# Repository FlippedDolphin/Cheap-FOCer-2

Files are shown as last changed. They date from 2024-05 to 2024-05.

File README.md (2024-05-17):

# Cheap FOCer 2 (v1.0)

Low-Cost(around $120 for 5 boards and components) Motor Controller based on the VESC 6

***** caution *******

This is a custom VESC for OpenFFBoard based On Cheap FOCer 2(v1.0)

* Replaced the shunt registers for low current.

* Removed the useless IMU.

* Cleaned up HALL/Encoder lines(for ABN) and COMM lines(for BiSS-C)
  for high frequency signals.(I tested COMM lines only.)

* Added OVP(over voltage protector) for PSU usage.

* Added POWER and MOTOR connector for easy plug.

* Max voltage 50V and max current is 14A.

U8 and J11 are unused, just for test purpose.

I placed JST connector for USB connection(USB1). The normal USB-C connector is J2, but it costs a little more. You can select J2/USB1(If use USB1, you need a converter from USB I/F to JST PH connector. I used cheap USB hub pcb).

A sample BOM and Position are in prodction folder.

bom.org.csv and position.org.csv are come from KiCad.

I used bom.csv and bom.lcsc.csv to order JLCPCB and LCSC respectively.

When I ordered the PCB and parts, I have already had some parts, so my order is minimum.
You need adjust the BOMS for your needs.

I used position.csv for JLCPCB order because original one from Kicad has errors for some parts. You need to check the position when you order yours.

## Warning

* This board has been bench tested with MIGE motor(130st-m10010 and 90ST-M04025) and BiSS-C encoder.
 Hardware or firmware flaws could still exist and affect user operation.
* You are liable for any and all controllers built using this design. This product is intended for hobbyists and not intended for commercial use.
* Do not ask the original auther of Cheap FOCer 2 about this board. He has no responsibility about this board at all.

Licens is followd by the parent project.

## Firmware

The firmware for this board is my bdlc repository with branch "Custom_CFOC2_OpenFFBoard". The Target is "Cheap_FOCer_2_005_nl".

***** caution *******

Front and Back:

 

Pin outs:


## License

Cheap FOCer 2 is licensed under the Creative Commons Attribution-ShareAlike 4.0 International License. To view a copy of this license, visit <http://creativecommons.org/licenses/by-sa/4.0/.>

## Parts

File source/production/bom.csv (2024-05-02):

Designator | Footprint | Quantity | Value | LCSC Part #
C1 | C0603 | 1 | 100nF | C14663
C10, C14 | 603 | 2 | 15p | C1644
C11, C13, C15, C16, C17, C18, C19, C47, C7, C8, C9 | 603 | 11 | 2.2u | C23630
C12, C2, C20, C24, C35, C43, C6 | 603 | 7 | 100n | C14663
C21, C23, C26, C28, C39, C4, C40, C66, C67 | 603 | 9 | 1nF | C1588
C22, C25, C30, C32, C44 | 603 | 5 | 2.2uF | C23630
C27 | 603 | 1 | 6.8n | C1631
C29 | 603 | 1 | 150p | C1594
C3 | 603 | 1 | .01uF | C57112
C31 | 603 | 1 | 22n | C21122
C33, C42 | 1210 | 2 | 4.7uF, 100V | C385986
C34 | 603 | 1 | 15nF | C1596
C36, C37, C38, C41 | 603 | 4 | 220n | C21120
C45, C46, C48, C49, C50, C51 | 805 | 6 | 22uf | C45783
C5 | 603 | 1 | 0.1u | C14663
C52, C53, C59, C60 | 603 | 4 | 2.2nF | C1604
C55, C56, C63, C64, C68, C69 | 805 | 6 | 4.7nF, 100V | C565636
C58, C61, C62 | 2220 | 3 | 10uF, 100V | C153035
C70, C71 | C1206 | 2 | 22uF | C77091
D1, D2 | SOT-363_SC-70-6 | 2 | SMF05CT1G | C15879
D10, D11, D12, D13, D14, D15 | D_SOD-323 | 6 | D_Schottky | C313457
D16 | SMA_L4.3-W2.6-LS5.2-RD | 1 | SS34 | C8678
D3 | 603 | 1 | RED | C2286
D4 | 603 | 1 | GRN | C72043
D5 | 603 | 1 | BLU | C965807
D6 | D_SMA | 1 | 100v, 1A | C224219
D7 | D_SMB | 1 | D_TVS | C78395
D8 | TO-220-2_Horizontal_TabUp | 1 | STTH3010DTO-220AC_STM | C73865
D9 | SODFL3618X110N | 1 | GOODWORK K110 | C908663
L1 | L_Taiyo-Yuden_NR-60xx_HandSoldering | 1 | 22u | C266430
L2 | IND-SMD_L7.0-W6.8 | 1 | 22uH | C27442
NTC1 | 603 | 1 | NTC 10k | C76589
Q10, Q11, Q2, Q3, Q6, Q7 | SOT-23 | 6 | Q_PNP_BCE | C8542
R1, R2 | R0603 | 2 | 5.1k | C23186
R10, R15, R16, R17, R29, R37, R39, R41, R5 | 603 | 9 | 2k2 | C4190
R11, R8, R9 | 603 | 3 | 100R | C22775
R12, R13 | 603 | 2 | 60 | C25196
R14, R18, R19, R20, R22, R23, R30, R32 | 603 | 8 | 10k | C25804
R21, R33, R34 | 603 | 3 | 1.5k | C22843
R24, R25, R31 | 603 | 3 | 1k | C21190
R26 | 603 | 1 | 3.3k | C22978
R27 | 603 | 1 | 18k | C25810
R28 | 603 | 1 | 15k | C22809
R3 | 603 | 1 | 0R | C3017805
R35 | 603 | 1 | 220k | C22961
R36, R38, R4, R40 | 603 | 4 | 39k | C23153
R42, R44 | RESC2012X65 | 2 | 20k | C114233
R43, R45 | RESC2012X65 | 2 | 1k | C100046
R46, R47, R49, R86 | RESC2012X65 | 4 | 10k | C100047
R48, R89 | RESC2012X65 | 2 | 560 | C137421
R50, R51, R62, R63, R74, R75 | 603 | 6 | 4.7R | C23164
R52, R53, R64, R65, R76, R77 | 805 | 6 | 4.7R | C17675
R54, R55, R66, R67, R78, R79 | 603 | 6 | 4.7k | C23162
R56, R57, R68, R69, R80, R81 | R_2512_Yageo_big_pads | 6 | 0.01R | C2903468
R58, R59, R60, R61, R70, R71, R72, R73, R82, R83, R84, R85 | 805 | 12 | 10R | C17415
R6, R7 | 603 | 2 | 22R | C23345
R87 | RESC2012X65 | 1 | 62K | C137415
R88 | RESC2012X65 | 1 | 3k3 | C114222
U1 | SOIC-8_3.9x4.9mm_P1.27mm | 1 | TJA1051T/3/1J | C38695
U2 | LQFP-64_10x10mm_P0.5mm | 1 | STM32F405RGT6 | C15742
U3 | SOIC-8_3.9x4.9mm_P1.27mm | 1 | TP2604-SR | C126446
U4 | HTSSOP-56-1EP_6.1x14mm_P0.5mm_EP3.61x6.35mm | 1 | DRV8301 | C98969
U5 | SOT-223-3_TabPin2 | 1 | AMS1117-3.3 | C6186
U7 | SOT-23-6_L2.9-W1.6-P0.95-LS2.8-BL(MT3608) | 1 | MT3608 | C84817
X1 | Crystal_SMD_5032-2Pin_5.0x3.2mm | 1 | 8MHz 10ppm (X50328MSB2GI) | C115962

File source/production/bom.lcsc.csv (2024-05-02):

Designator | Footprint | Quantity | Value | LCSC Part # | Bottom | 所有
C54, C57, C65 | CP_10x20mm_hor_with_model_mirrored_less_silk | 3 | 330u, 63V | C437643
D8 | TO-220-2_Horizontal_TabUp | 1 | STTH3010DTO-220AC_STM | C73865
J4 | CONN-TH_2P-P5.08_1757242 | 1 | Conn_01x02 | C90074
J8 | CONN-TH_MSTBA2.5-4-G-5.08 | 1 | MotorPower | C90076
Q1 | TO-247-3_Horizontal_TabUp | 1 | FGH40N60SFDTU | C49514
Q10, Q11, Q2, Q3, Q6, Q7 | SOT-23 | 6 | Q_PNP_BCE | C8542
Q12, Q13, Q4, Q5, Q8, Q9 | TO-220-3_Horizontal_TabUp_no_hole | 6 | NCEP60T20 | C284868

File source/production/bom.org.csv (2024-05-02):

Designator | Footprint | Quantity | Value | LCSC Part #
C1 | C0603 | 1 | 100nF | C14663
C10, C14 | 0603 | 2 | 15p | C1644
C11, C13, C15, C16, C17, C18, C19, C47, C7, C8, C9 | 0603 | 11 | 2.2u | C23630
C12, C2, C20, C24, C35, C43, C6 | 0603 | 7 | 100n | C14663
C21, C23, C26, C28, C39, C4, C40, C66, C67 | 0603 | 9 | 1nF | C1588
C22, C25, C30, C32, C44 | 0603 | 5 | 2.2uF | C23630
C27 | 0603 | 1 | 6.8n | C1631
C29 | 0603 | 1 | 150p | C1594
C3 | 0603 | 1 | .01uF | C57112
C31 | 0603 | 1 | 22n | C21122
C33, C42 | 1210 | 2 | 4.7uF, 100V | C385986
C34 | 0603 | 1 | 15nF | C1596
C36, C37, C38, C41 | 0603 | 4 | 220n | C21120
C45, C46, C48, C49, C50, C51 | 0805 | 6 | 22uf | C45783
C5 | 0603 | 1 | 0.1u | C14663
C52, C53, C59, C60 | 0603 | 4 | 2.2nF | C1604
C54, C57, C65 | CP_10x20mm_hor_with_model_mirrored_less_silk | 3 | 330u, 63V | C437643
C55, C56, C63, C64, C68, C69 | 0805 | 6 | 4.7nF, 100V | C565636
C58, C61, C62 | 2220 | 3 | 10uF, 100V | C153035
C70, C71 | C1206 | 2 | 22uF | C77091
D1, D2 | SOT-363_SC-70-6 | 2 | SMF05CT1G | C15879
D10, D11, D12, D13, D14, D15 | D_SOD-323 | 6 | D_Schottky | C313457
D16 | SMA_L4.3-W2.6-LS5.2-RD | 1 | SS34 | C8678
D3 | 0603 | 1 | RED | C2286
D4 | 0603 | 1 | GRN | C72043
D5 | 0603 | 1 | BLU | C965807
D6 | D_SMA | 1 | 100v, 1A | C224219
D7 | D_SMB | 1 | D_TVS | C78395
D8 | TO-220-2_Horizontal_TabUp | 1 | STTH3010DTO-220AC_STM | C73865
D9 | SODFL3618X110N | 1 | GOODWORK K110 | C908663
F1, F2, F3 | Fiducial_1mm_Dia_2mm_Outer | 3 | Fiducial
H1, H2, H3, H4_3, H4_2, H4, H5, H6 | MountingHole_3.2mm_M3_ISO14580_Pad | 8 | MountingHole
H7 | Sam_J | 1 | SLJ
H8 | OSHW-Logo2_9.8x8mm_SilkScreen | 1 | Open Hardware Logo
H9 | KiCad-Logo2_5mm_SilkScreen | 1 | KiCAD Logo
J1 | JST_PH_B7B-PH-K_1x07_P2.00mm_Vertical | 1 | Conn_01x07
J10 | JST_PH_B2B-PH-K_1x02_P2.00mm_Vertical | 1 | On/Off
J11 | CONN-TH_1755736 | 1 | VESC_Vin | C480503
J12 | JST_PH_B2B-PH-K_1x02_P2.00mm_Vertical | 1 | PWR LED
J13 | JST_PH_S2B-PH-K_1x02_P2.00mm_Horizontal | 1 | E-Stop
J2 | GCT_USB4105-GF-A | 1 | USB4105-GF-A | C319148
J3, J7 | JST_PH_B2B-PH-K_1x02_P2.00mm_Vertical | 2 | Conn_01x02
J4 | CONN-TH_2P-P5.08_1757242 | 1 | Conn_01x02 | C90074
J5 | JST_PH_B3B-PH-K_1x03_P2.00mm_Vertical_hybrid | 1 | Conn_01x03
J6 | PinHeader_1x02_P2.54mm_Vertical | 1 | Conn_01x03
J8 | CONN-TH_MSTBA2.5-4-G-5.08 | 1 | MotorPower | C90076
J9 | PinHeader_2x05_P2.00mm_Vertical | 1 | UNUSED MCU PINS
JP1 | SolderJumper-3_P1.3mm_Open_RoundedPad1.0x1.5mm_NumberLabels | 1 | SolderJumper_3_Open
L1 | L_Taiyo-Yuden_NR-60xx_HandSoldering | 1 | 22u | C266430
L2 | IND-SMD_L7.0-W6.8 | 1 | 22uH | C27442
NT1, NT2, NT3, NT4, NT5, NT6 | NetTie-2_SMD_Pad0.5mm | 6 | Net-Tie_2
NTC1 | 0603 | 1 | NTC 10k | C76589
P1 | JST_PH_B6B-PH-K_1x06_P2.00mm_Vertical | 1 | HALL/Encoder
P2 | JST_PH_B5B-PH-K_1x05_P2.00mm_Vertical | 1 | Conn_01x05_PH_SWIO
Q1 | TO-247-3_Horizontal_TabUp | 1 | FGH40N60SFDTU | C49514
Q10, Q11, Q2, Q3, Q6, Q7 | SOT-23 | 6 | Q_PNP_BCE | C8542
Q12, Q13, Q4, Q5, Q8, Q9 | TO-220-3_Horizontal_TabUp_no_hole | 6 | NCEP60T20 | C284868
R1, R2 | R0603 | 2 | 5.1k | C23186
R10, R15, R16, R17, R29, R37, R39, R41, R5 | 0603 | 9 | 2k2 | C4190
R11, R8, R9 | 0603 | 3 | 100R | C22775
R12, R13 | 0603 | 2 | 60 | C25196
R14, R18, R19, R20, R22, R23, R30, R32 | 0603 | 8 | 10k | C25804
R21, R33, R34 | 0603 | 3 | 1.5k | C22843
R24, R25, R31 | 0603 | 3 | 1k | C21190
R26 | 0603 | 1 | 3.3k | C22978
R27 | 0603 | 1 | 18k | C25810
R28 | 0603 | 1 | 15k | C22809
R3 | 0603 | 1 | 0R | C3017805
R35 | 0603 | 1 | 220k | C22961
R36, R38, R4, R40 | 0603 | 4 | 39k | C23153
R42, R44 | RESC2012X65 | 2 | 20k | C114233
R43, R45 | RESC2012X65 | 2 | 1k | C100046
R46, R47, R49, R86 | RESC2012X65 | 4 | 10k | C100047
R48, R89 | RESC2012X65 | 2 | 560 | C137421
R50, R51, R62, R63, R74, R75 | 0603 | 6 | 4.7R | C23164
R52, R53, R64, R65, R76, R77 | 0805 | 6 | 4.7R | C17675
R54, R55, R66, R67, R78, R79 | 0603 | 6 | 4.7k | C23162
R56, R57, R68, R69, R80, R81 | R_2512_Yageo_big_pads | 6 | 0.01R | C2903468
R58, R59, R60, R61, R70, R71, R72, R73, R82, R83, R84, R85 | 0805 | 12 | 10R | C17415
R6, R7 | 0603 | 2 | 22R | C23345
R87 | RESC2012X65 | 1 | 62K | C137415
R88 | RESC2012X65 | 1 | 3k3 | C114222
TP1 | TP1X01 | 1 | 12V
TP2 | TP1X01 | 1 | BR-
TP3 | TP1X01 | 1 | BR+
U1 | SOIC-8_3.9x4.9mm_P1.27mm | 1 | TJA1051T/3/1J | C38695
U2 | LQFP-64_10x10mm_P0.5mm | 1 | STM32F405RGT6 | C15742
U3 | SOIC-8_3.9x4.9mm_P1.27mm | 1 | TP2604-SR | C126446
U4 | HTSSOP-56-1EP_6.1x14mm_P0.5mm_EP3.61x6.35mm | 1 | DRV8301 | C98969
U5 | SOT-223-3_TabPin2 | 1 | AMS1117-3.3 | C6186
U6 | DIP794W45P254L959H508Q8 | 1 | LM358P | C5213
U7 | SOT-23-6_L2.9-W1.6-P0.95-LS2.8-BL(MT3608) | 1 | MT3608 | C84817
U8 | MT3068_Module | 1 | MT3608_Modle
USB1 | CONN-TH_B3B-PH-K-S | 1 | Conn_01x03 | C131339
X1 | Crystal_SMD_5032-2Pin_5.0x3.2mm | 1 | 8MHz 10ppm (X50328MSB2GI) | C115962

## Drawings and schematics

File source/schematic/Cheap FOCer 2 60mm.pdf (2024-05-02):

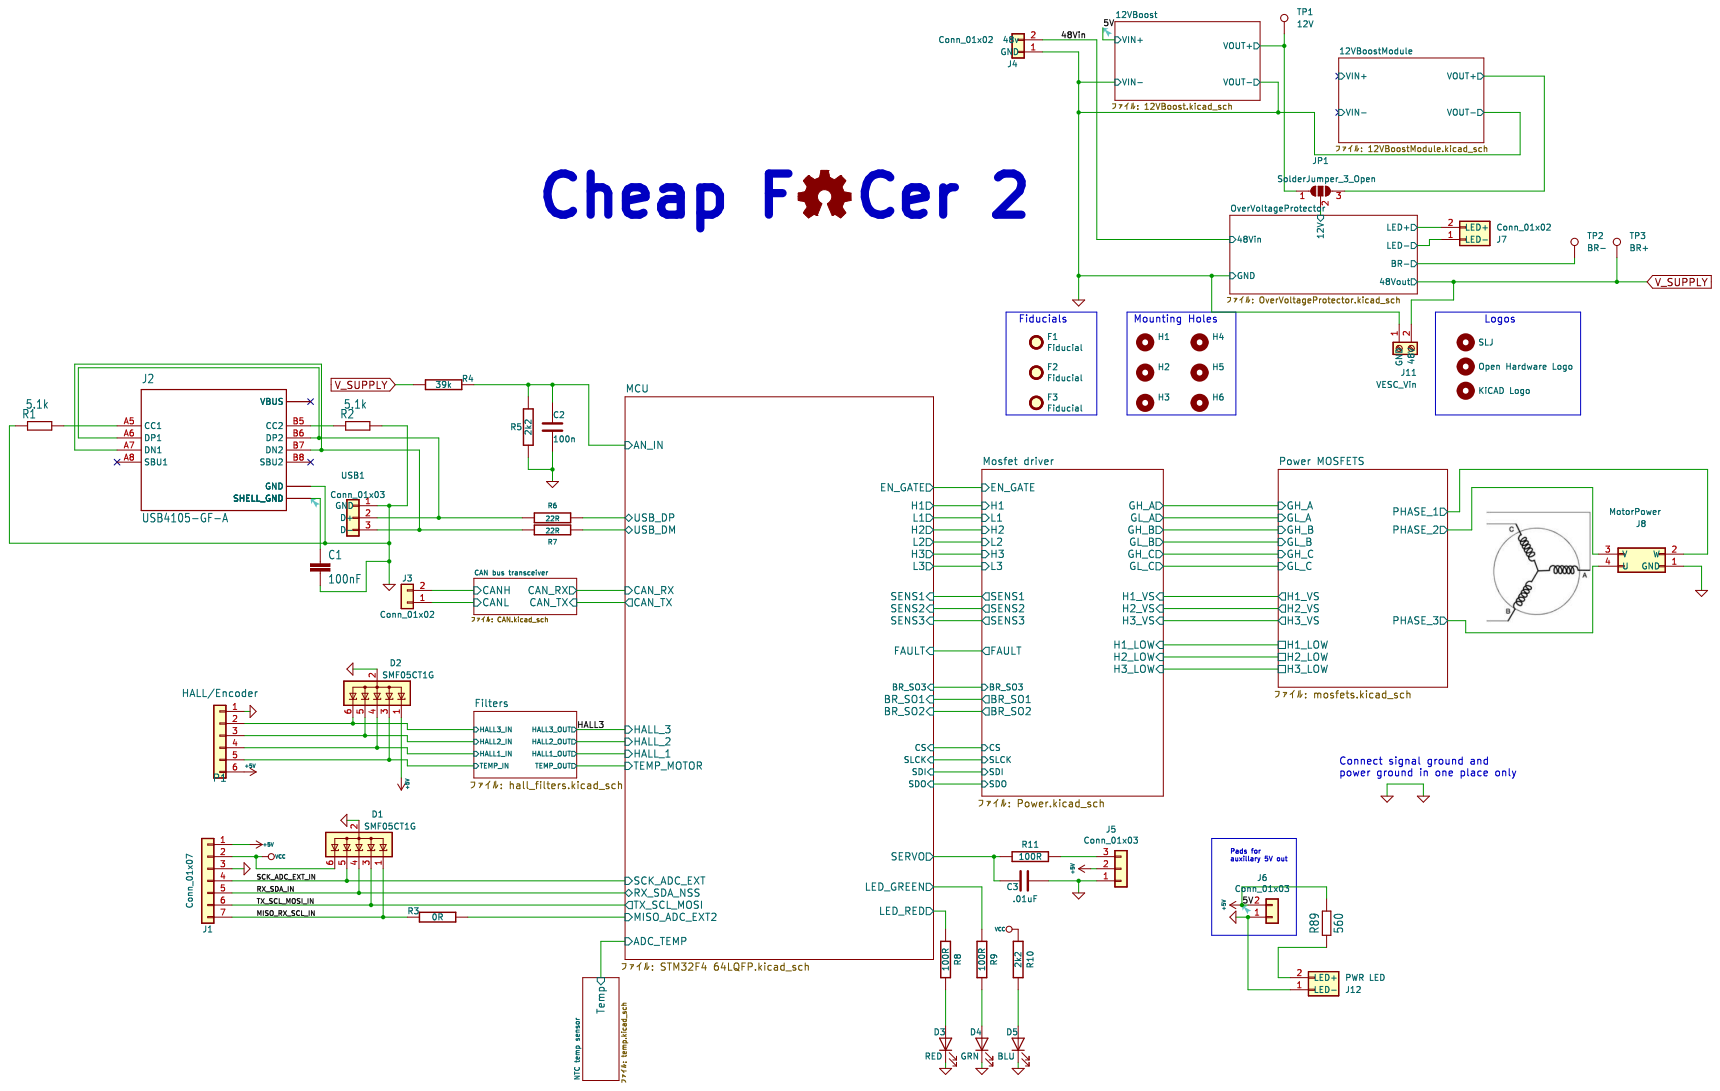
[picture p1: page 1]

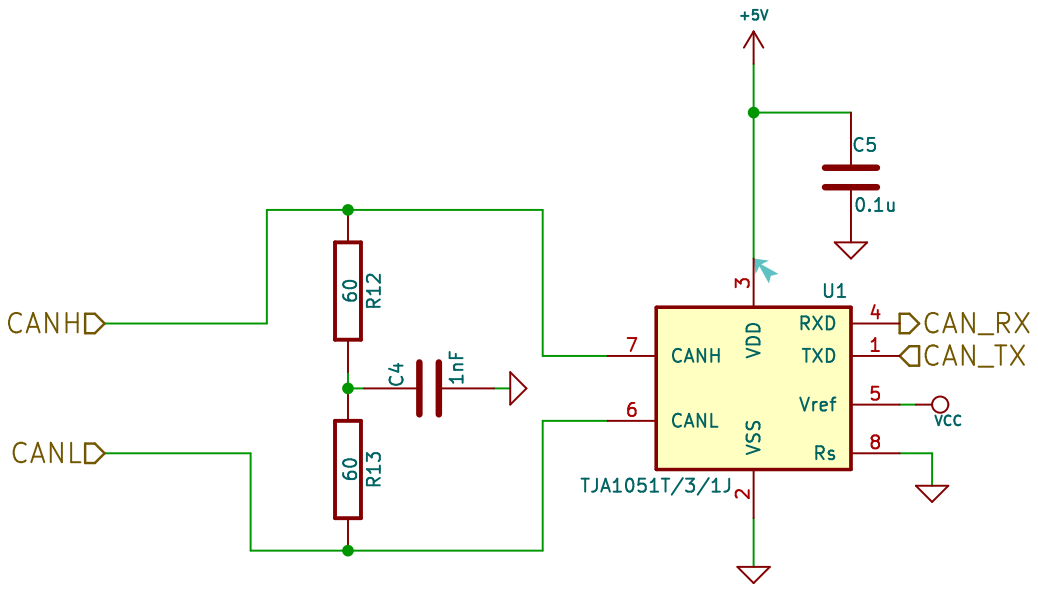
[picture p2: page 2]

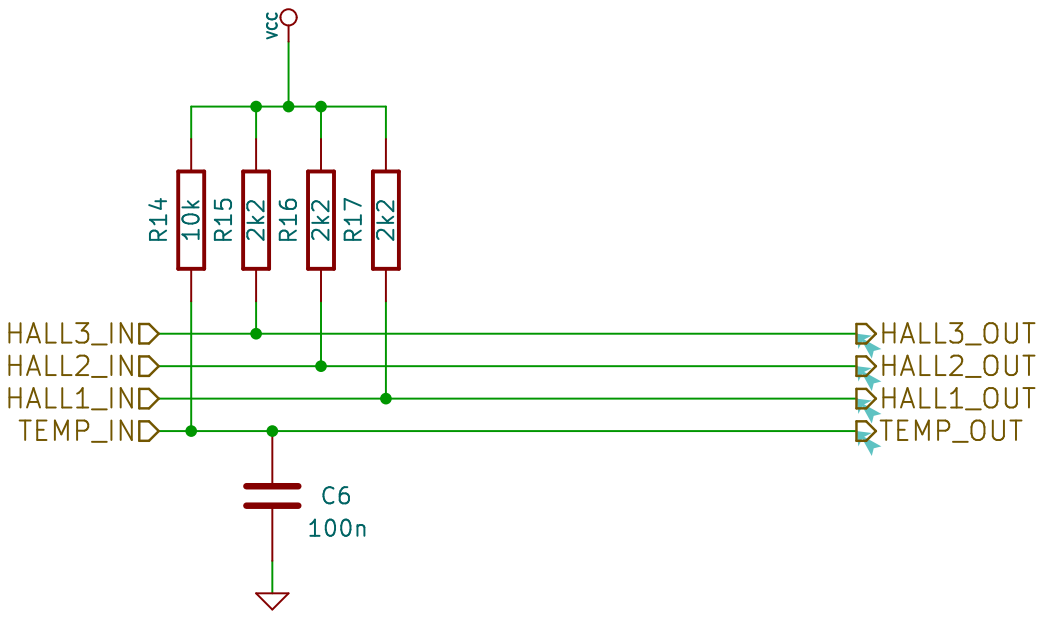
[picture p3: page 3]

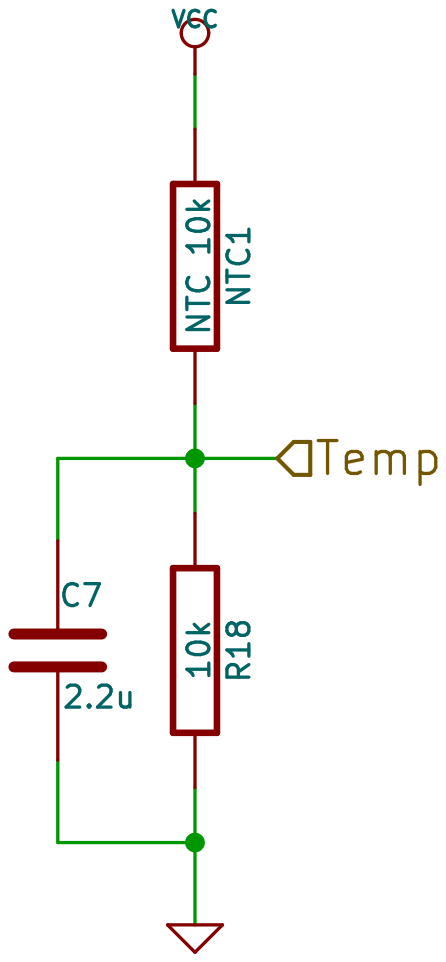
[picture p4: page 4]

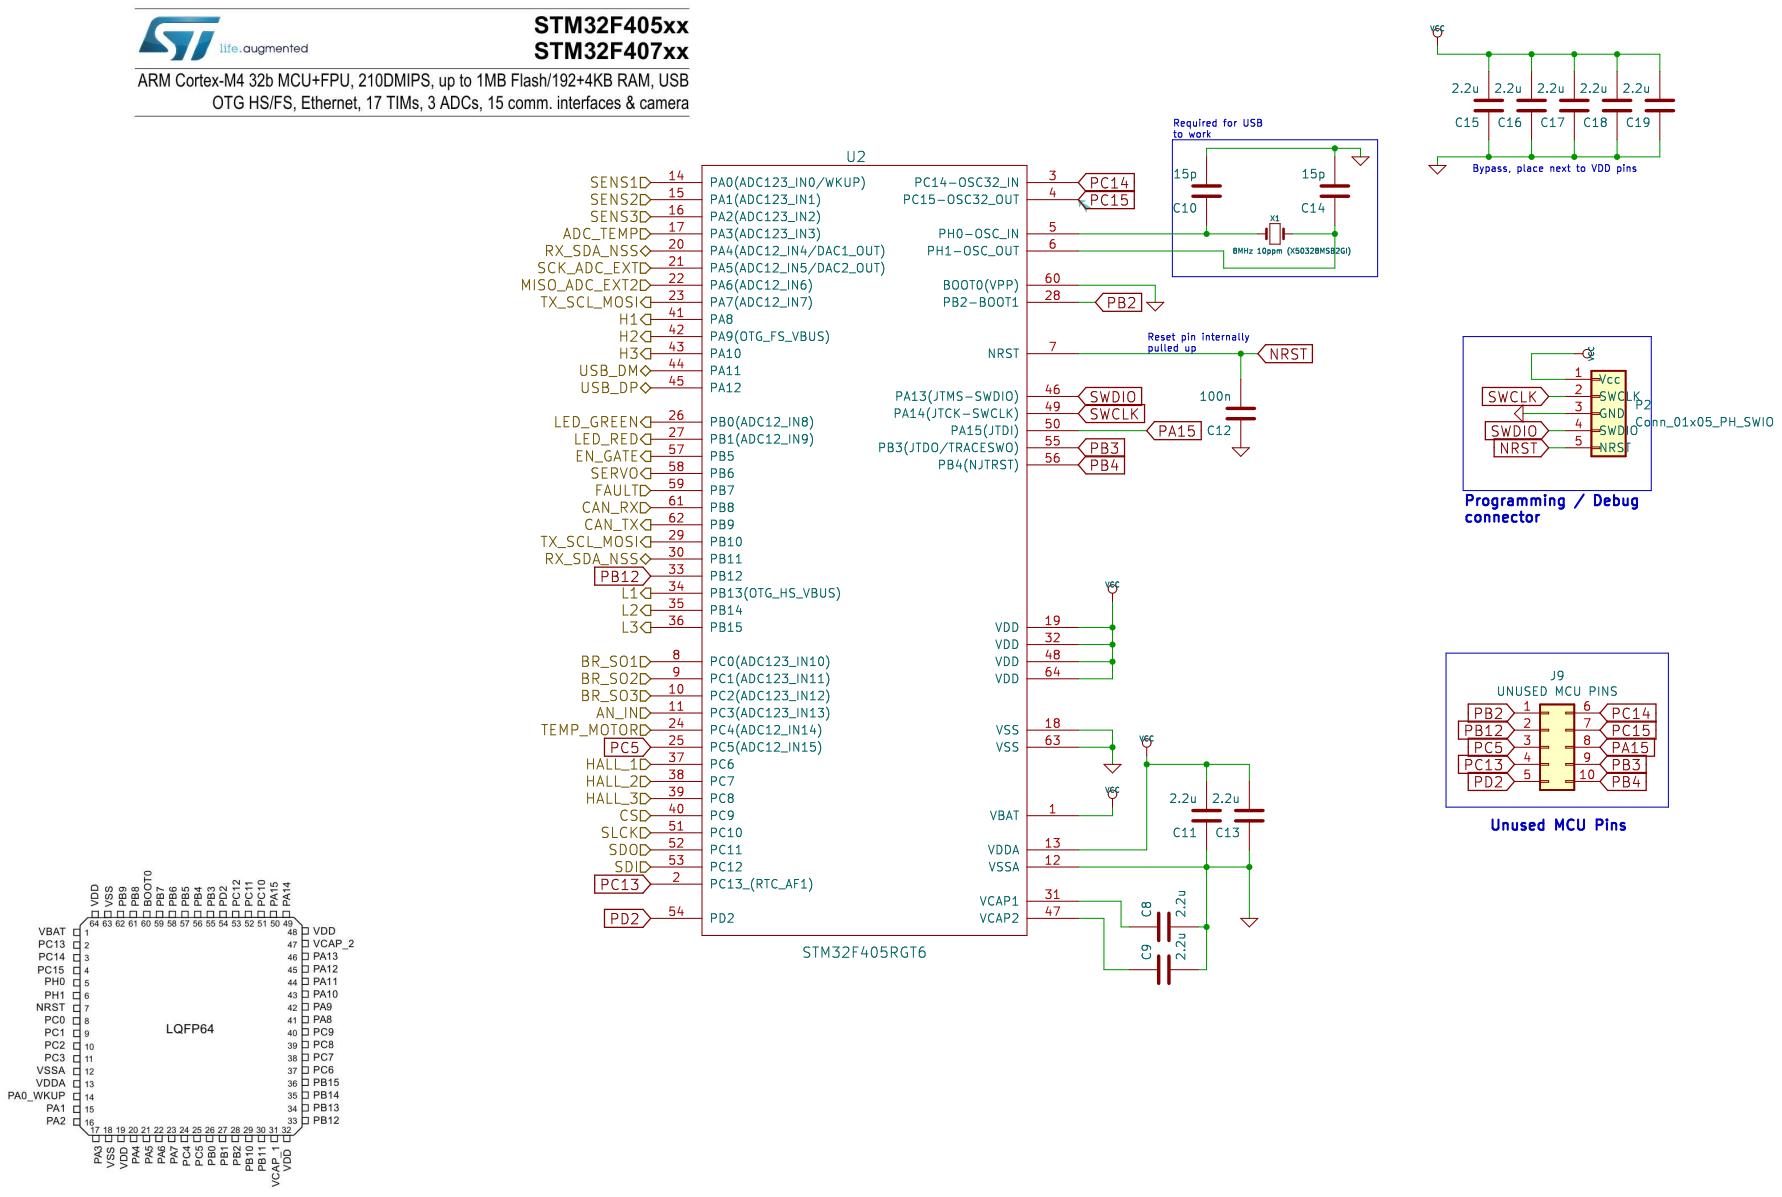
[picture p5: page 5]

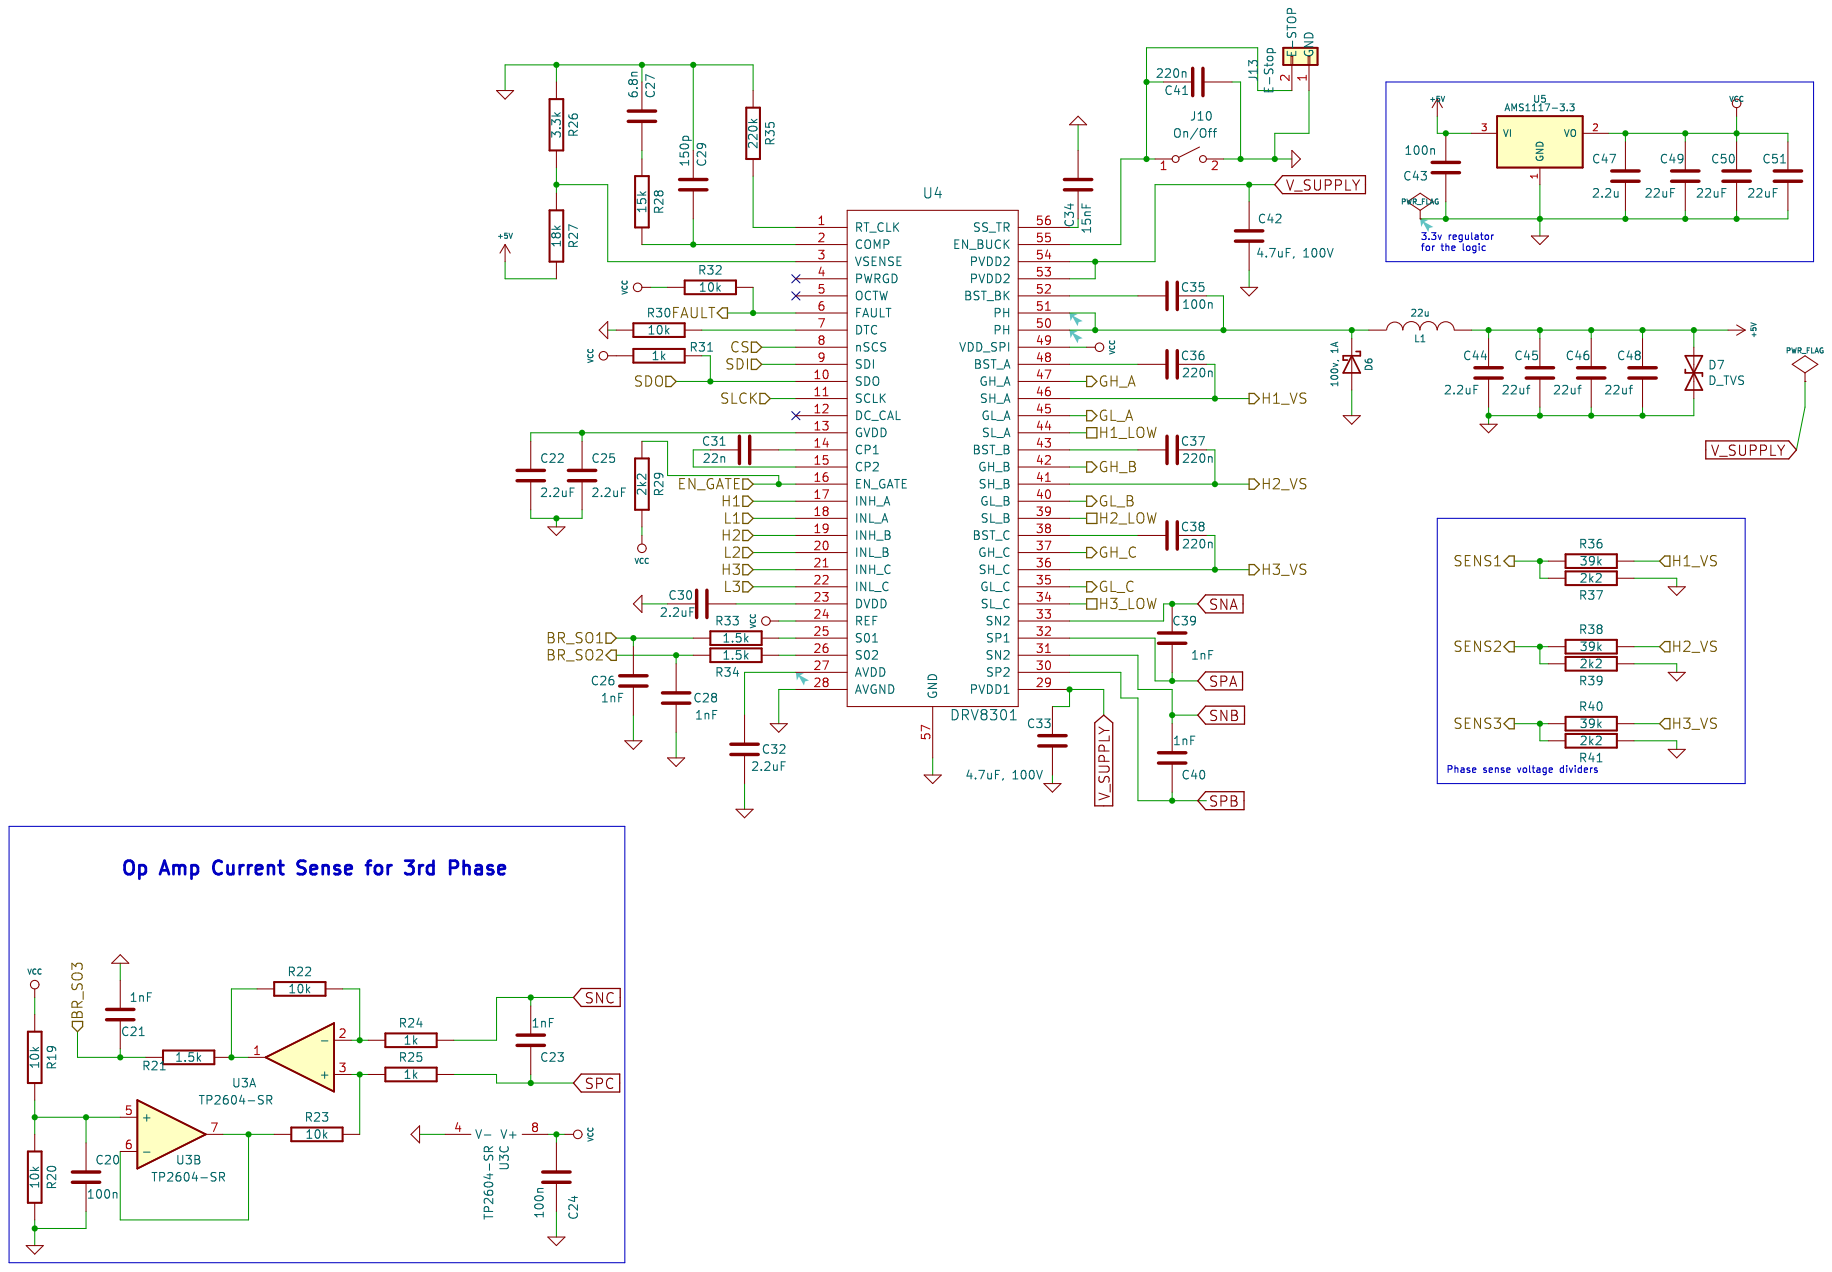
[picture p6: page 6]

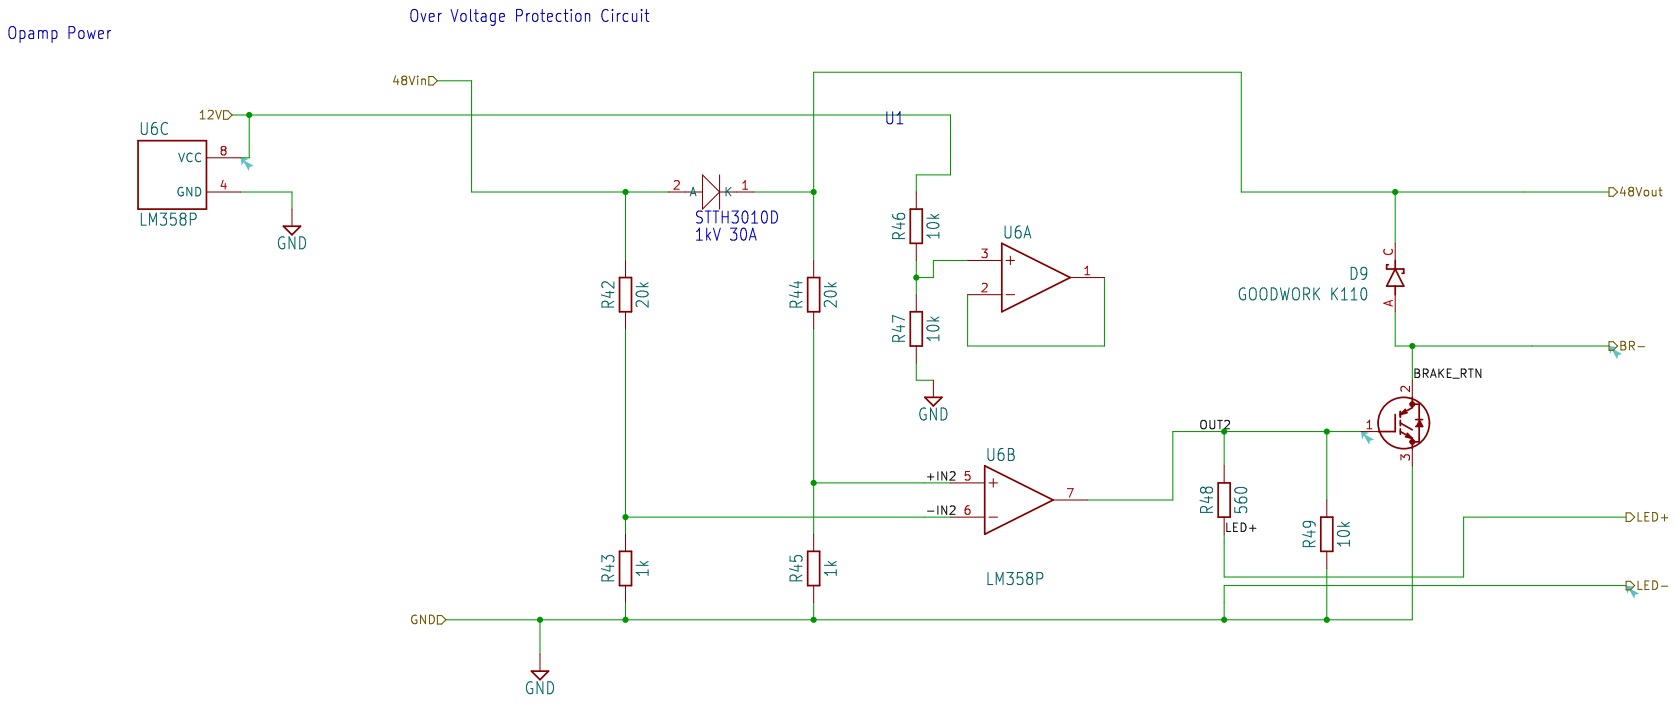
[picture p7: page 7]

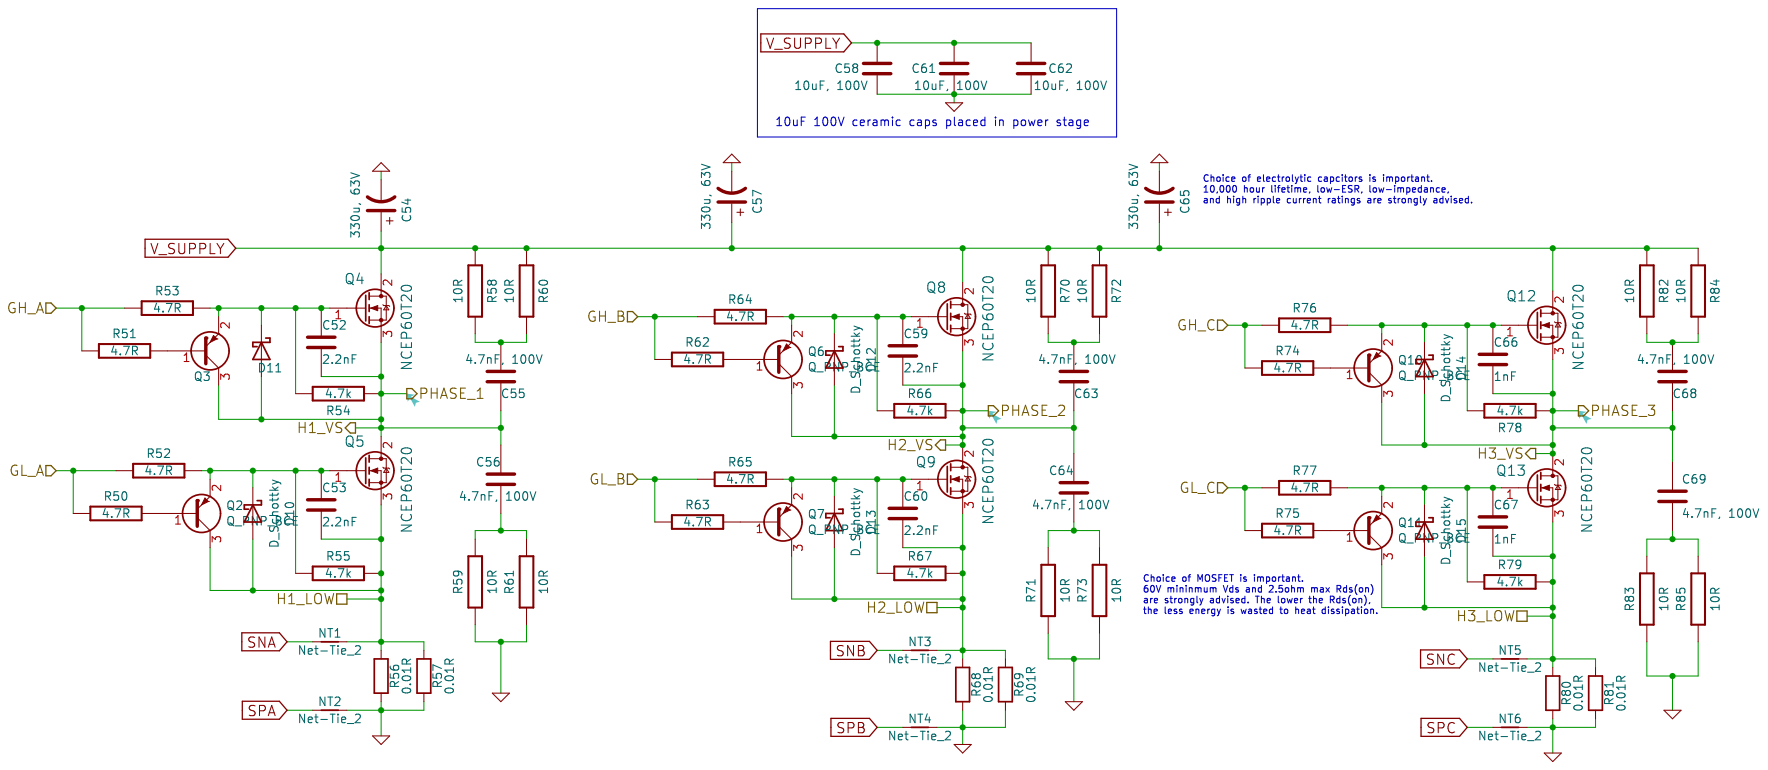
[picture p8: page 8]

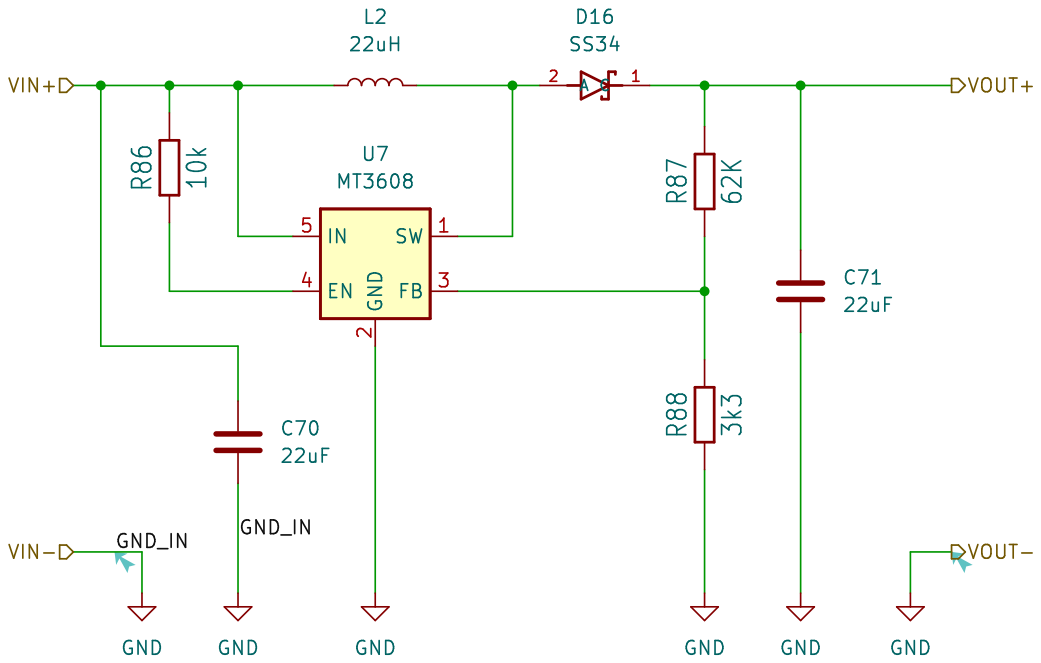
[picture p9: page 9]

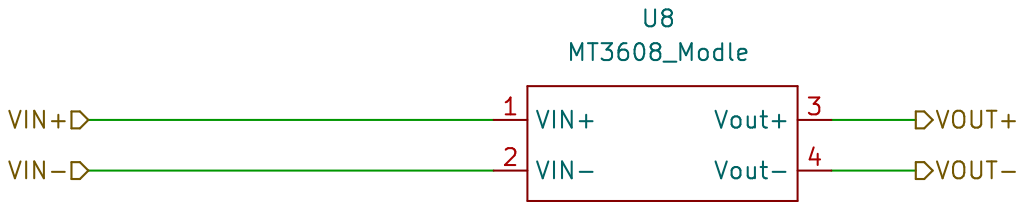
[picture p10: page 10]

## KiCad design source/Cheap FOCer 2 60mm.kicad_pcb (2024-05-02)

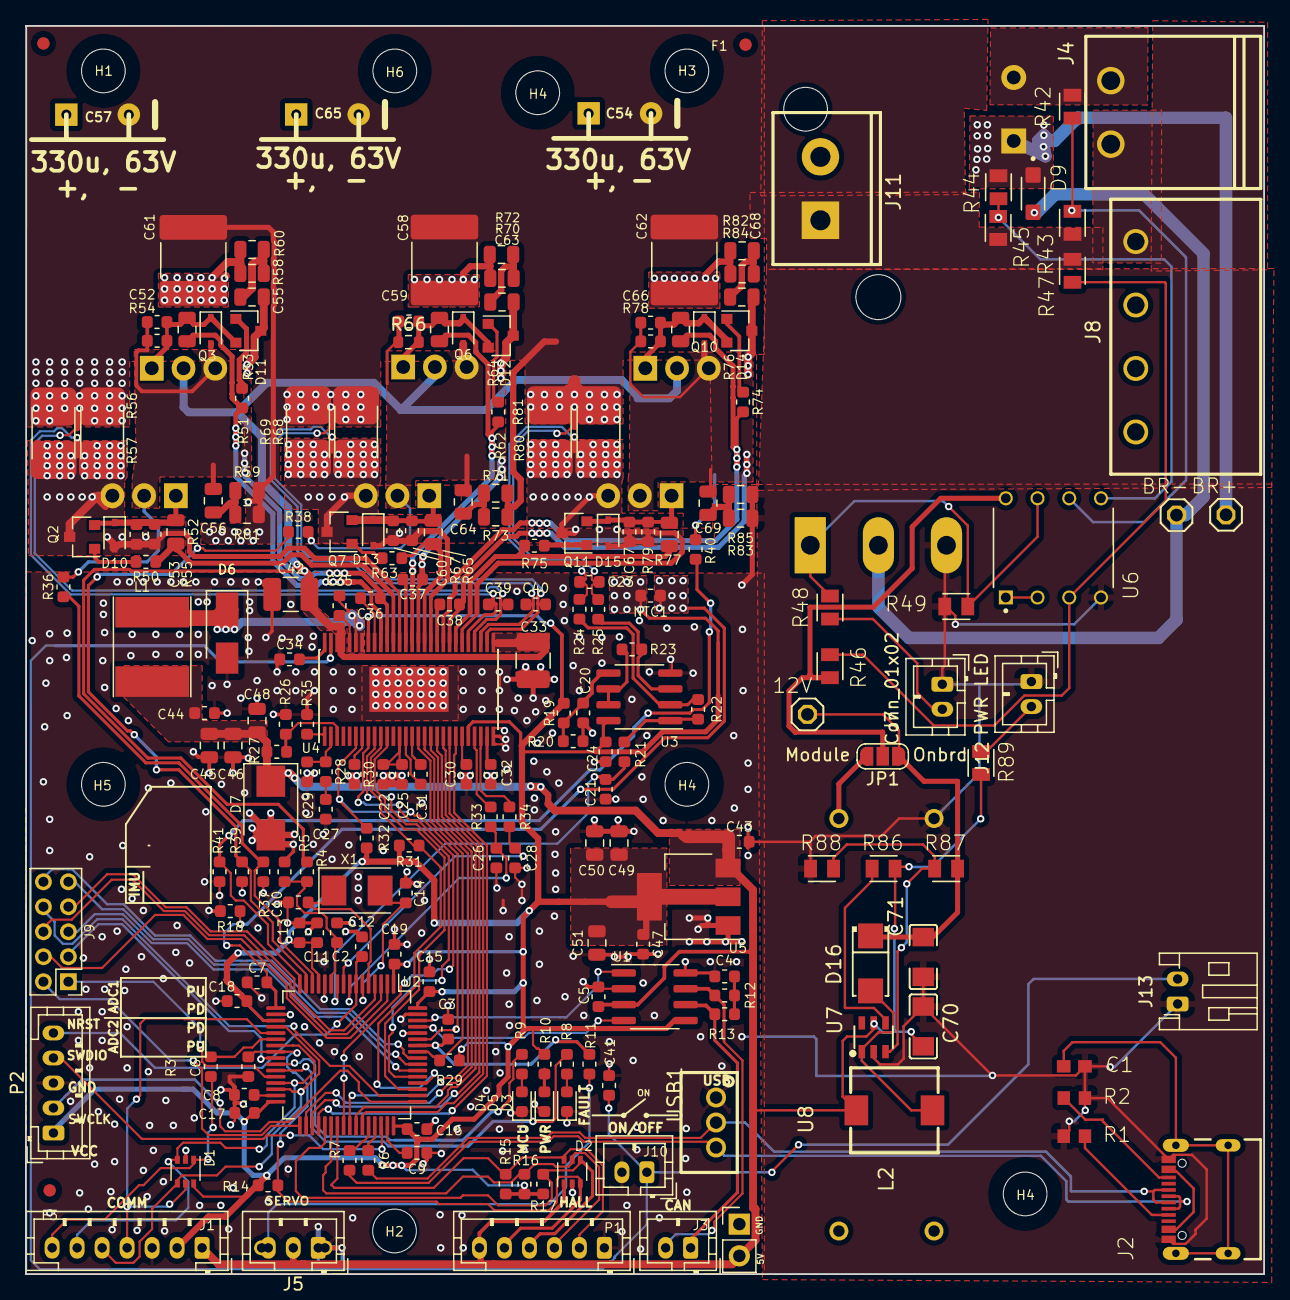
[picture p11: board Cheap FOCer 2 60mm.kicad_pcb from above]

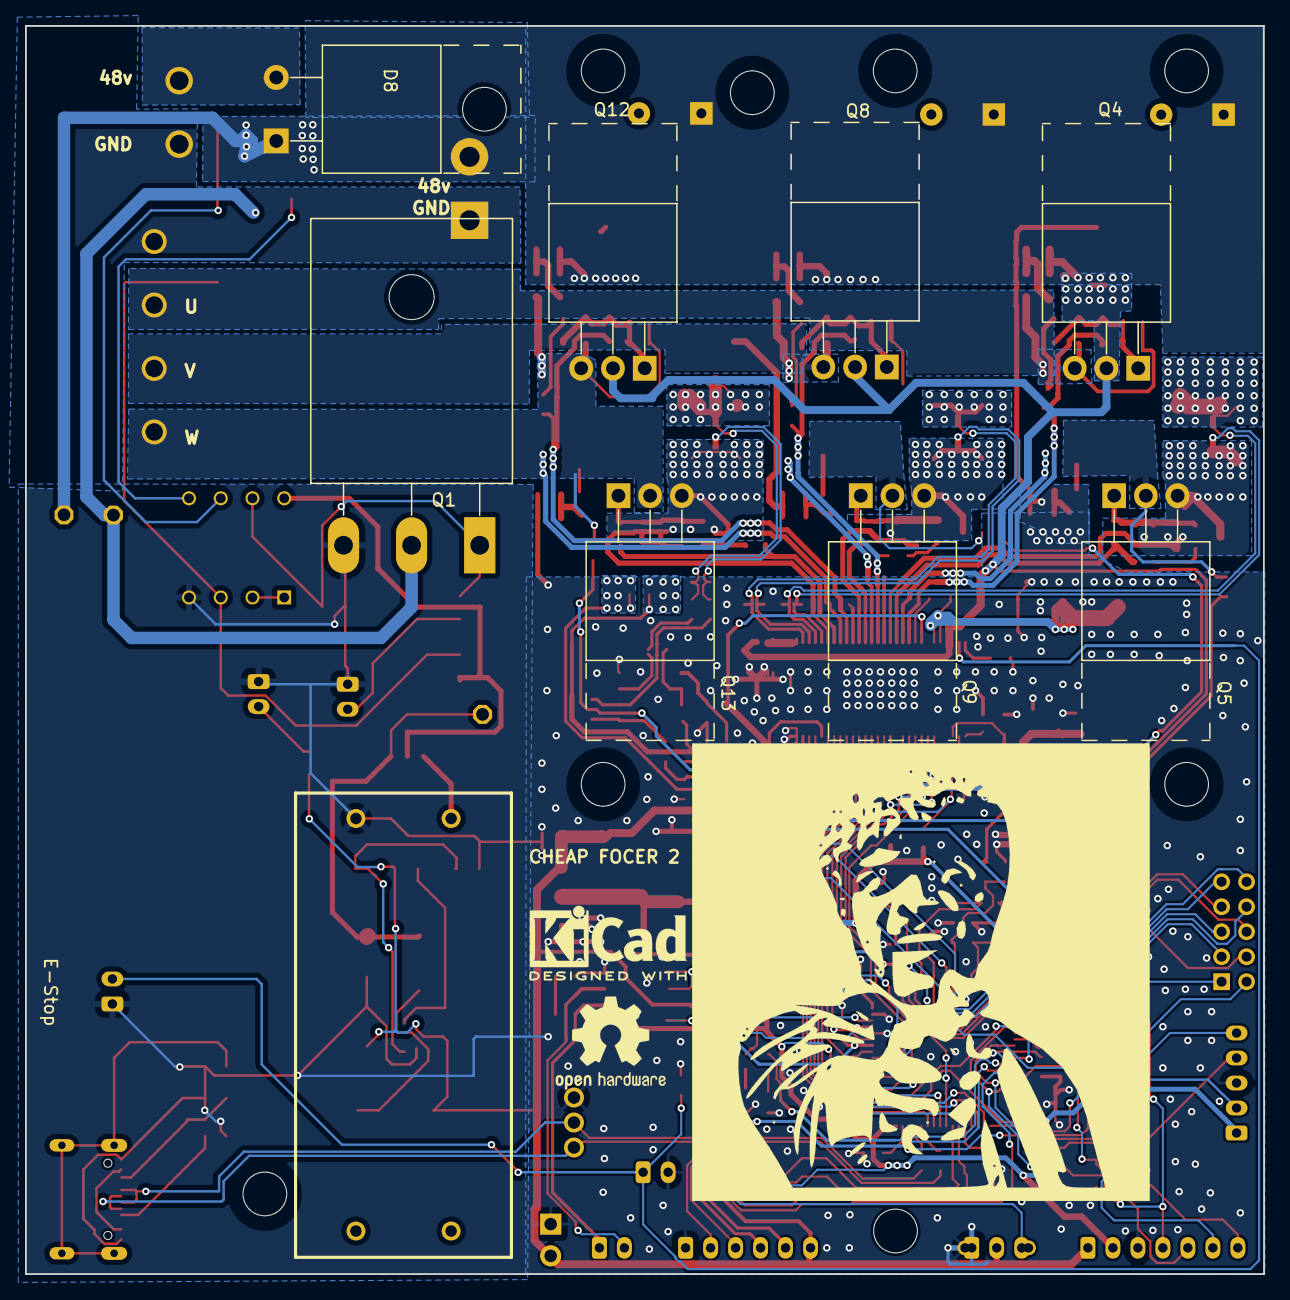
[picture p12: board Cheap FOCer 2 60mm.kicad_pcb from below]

Board: 2 copper layers, 99.1 x 99.9 mm, 241 parts (11 on the bottom side), 144 nets.

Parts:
C1: 100nF; C0603
C2, C6, C12, C20, C24, C35, C43: 100n; C_0603_1608Metric
C3: .01uF; C_0603_1608Metric
C4, C21, C23, C26, C28, C39, C40, C66, C67: 1nF; C_0603_1608Metric
C5: 0.1u; C_0603_1608Metric
C7, C8, C9, C11, C13, C15, C16, C17, C18, C19, C47: 2.2u; C_0603_1608Metric
C10, C14: 15p; C_0603_1608Metric
C22, C25, C30, C32, C44: 2.2uF; C_0603_1608Metric
C27: 6.8n; C_0603_1608Metric
C29: 150p; C_0603_1608Metric
C31: 22n; C_0603_1608Metric
C33, C42: 4.7uF, 100V; C_1210_3225Metric_Pad1.42x2.65mm_HandSolder
C34: 15nF; C_0603_1608Metric
C36, C37, C38, C41: 220n; C_0603_1608Metric
C45, C46, C48: 22uf; C_0805_2012Metric
C49, C50, C51: 22uF; C_0805_2012Metric
C52, C53, C59, C60: 2.2nF; C_0603_1608Metric
C54, C57, C65: 330u, 63V; CP_10x20mm_hor_with_model_mirrored_less_silk
C55, C56, C63, C64, C68, C69: 4.7nF, 100V; C_0805_2012Metric
C58, C61, C62: 10uF, 100V; C_2220_5650Metric_Pad1.97x5.40mm_HandSolder
C70, C71: 22uF; C1206
D1, D2: SMF05CT1G; SOT-363_SC-70-6
D3: RED; LED_0603_1608Metric
D4: GRN; LED_0603_1608Metric
D5: BLU; LED_0603_1608Metric
D6: 100v, 1A; D_SMA
D7: D_TVS; D_SMB
D8: STTH3010DTO-220AC_STM; TO-220-2_Horizontal_TabUp
D9: GOODWORK K110; SODFL3618X110N
D10, D11, D12, D13, D14, D15: D_Schottky; D_SOD-323
D16: SS34; SMA_L4.3-W2.6-LS5.2-RD
F1, F2, F3: Fiducial; Fiducial_1mm_Dia_2mm_Outer
H1, H2, H3, H4, H4#2, H4#3, H5, H6: MountingHole; MountingHole_3.2mm_M3_ISO14580_Pad
H7: SLJ; Sam_J
H8: Open Hardware Logo; OSHW-Logo2_9.8x8mm_SilkScreen
H9: KiCAD Logo; KiCad-Logo2_5mm_SilkScreen
J1: Conn_01x07; JST_PH_B7B-PH-K_1x07_P2.00mm_Vertical
J2: USB4105-GF-A; GCT_USB4105-GF-A
J3, J7: Conn_01x02; JST_PH_B2B-PH-K_1x02_P2.00mm_Vertical
J4: Conn_01x02; CONN-TH_2P-P5.08_1757242
J5: Conn_01x03; JST_PH_B3B-PH-K_1x03_P2.00mm_Vertical_hybrid
J6: Conn_01x03; PinHeader_1x02_P2.54mm_Vertical
J8: MotorPower; CONN-TH_MSTBA2.5-4-G-5.08
J9: UNUSED MCU PINS; PinHeader_2x05_P2.00mm_Vertical
J10: On/Off; JST_PH_B2B-PH-K_1x02_P2.00mm_Vertical
J11: VESC_Vin; CONN-TH_1755736
J12: PWR LED; JST_PH_B2B-PH-K_1x02_P2.00mm_Vertical
J13: E-Stop; JST_PH_S2B-PH-K_1x02_P2.00mm_Horizontal
JP1: SolderJumper_3_Open; SolderJumper-3_P1.3mm_Open_RoundedPad1.0x1.5mm_NumberLabels
L1: 22u; L_Taiyo-Yuden_NR-60xx_HandSoldering
L2: 22uH; IND-SMD_L7.0-W6.8
NT1, NT2, NT3, NT4, NT5, NT6: Net-Tie_2; NetTie-2_SMD_Pad0.5mm
NTC1: NTC 10k; R_0603_1608Metric
P1: HALL/Encoder; JST_PH_B6B-PH-K_1x06_P2.00mm_Vertical
P2: Conn_01x05_PH_SWIO; JST_PH_B5B-PH-K_1x05_P2.00mm_Vertical
Q1: FGH40N60SFDTU; TO-247-3_Horizontal_TabUp
Q2, Q3, Q6, Q7, Q10, Q11: Q_PNP_BCE; SOT-23
Q4, Q5, Q8, Q9, Q12, Q13: NCEP60T20; TO-220-3_Horizontal_TabUp_no_hole
R1, R2: 5.1k; R0603
R3: 0R; R_0603_1608Metric
R4, R36, R38, R40: 39k; R_0603_1608Metric
R5, R10, R15, R16, R17, R29, R37, R39, R41: 2k2; R_0603_1608Metric
R6, R7: 22R; R_0603_1608Metric
R8, R9, R11: 100R; R_0603_1608Metric
R12, R13: 60; R_0603_1608Metric
R14, R18, R19, R20, R22, R23, R30, R32: 10k; R_0603_1608Metric
R21, R33, R34: 1.5k; R_0603_1608Metric
R24, R25, R31: 1k; R_0603_1608Metric
R26: 3.3k; R_0603_1608Metric
R27: 18k; R_0603_1608Metric
R28: 15k; R_0603_1608Metric
R35: 220k; R_0603_1608Metric
R42, R44: 20k; RESC2012X65
R43, R45: 1k; RESC2012X65
R46, R47, R49, R86: 10k; RESC2012X65
R48, R89: 560; RESC2012X65
R50, R51, R62, R63, R74, R75: 4.7R; R_0603_1608Metric
R52, R53, R64, R65, R76, R77: 4.7R; R_0805_2012Metric
R54, R55, R66, R67, R78, R79: 4.7k; R_0603_1608Metric
R56, R57, R68, R69, R80, R81: 0.01R; R_2512_Yageo_big_pads
R58, R59, R60, R61, R70, R71, R72, R73, R82, R83, R84, R85: 10R; R_0805_2012Metric
R87: 62K; RESC2012X65
R88: 3k3; RESC2012X65
TP1: 12V; TP1X01
TP2: BR-; TP1X01
TP3: BR+; TP1X01
U1: TJA1051T/3/1J; SOIC-8_3.9x4.9mm_P1.27mm
U2: STM32F405RGT6; LQFP-64_10x10mm_P0.5mm
U3: TP2604-SR; SOIC-8_3.9x4.9mm_P1.27mm
U4: DRV8301; HTSSOP-56-1EP_6.1x14mm_P0.5mm_EP3.61x6.35mm
U5: AMS1117-3.3; SOT-223-3_TabPin2
U6: LM358P; DIP794W45P254L959H508Q8
U7: MT3608; SOT-23-6_L2.9-W1.6-P0.95-LS2.8-BL(MT3608)
U8: MT3608_Modle; MT3068_Module
USB1: Conn_01x03; CONN-TH_B3B-PH-K-S
X1: 8MHz 10ppm (X50328MSB2GI); Crystal_SMD_5032-2Pin_5.0x3.2mm

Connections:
+5V: C5.1, C43.2, C44.2, C45.2, C46.2, C48.2, C70.1, D2.1 (K), D7.1 (A1), J1.1, J5.2, J6.2, L1.2, L2.1, P1.6, R27.1, R86.2, R89.2, U1.3 (VDD), U5.3 (VI), U7.5 (IN)
/12VBoost/VOUT+: C71.1, D16.1 (C), JP1.1 (A), R87.2, TP1.1
/12VBoostModule/VOUT+: JP1.3 (B), U8.3 (Vout+)
/48Vin: D8.2 (A), J4.2 (48v), R42.2
/CAN bus transceiver/CANH: J3.2, R12.1, U1.7 (CANH)
/CAN bus transceiver/CANL: J3.1, R13.2, U1.6 (CANL)
/CAN bus transceiver/CAN_RX: U1.4 (RXD), U2.61 (PB8)
/CAN bus transceiver/CAN_TX: U1.1 (TXD), U2.62 (PB9)
/Filters/HALL1_IN: D2.4 (K), P1.4, R17.1, U2.37 (PC6)
/Filters/HALL2_IN: D2.5 (K), P1.3, R16.1, U2.38 (PC7)
/Filters/TEMP_IN: C6.2, D2.3 (K), P1.5, R14.1, U2.24 (PC4(ADC12_IN14))
/HALL3: D2.6 (K), P1.2, R15.1, U2.39 (PC8)
/MCU/ADC_TEMP: C7.1, NTC1.2, R18.1, U2.17 (PA3(ADC123_IN3))
/MCU/AN_IN: C2.2, R4.2, R5.2, U2.11 (PC3(ADC123_IN13))
/MCU/BR_SO1: C26.2, R33.1, U2.8 (PC0(ADC123_IN10))
/MCU/BR_SO2: C28.2, R34.1, U2.9 (PC1(ADC123_IN11))
/MCU/BR_SO3: C21.2, R21.1, U2.10 (PC2(ADC123_IN12))
/MCU/CS: U2.40 (PC9), U4.8 (nSCS)
/MCU/EN_GATE: R29.1, U2.57 (PB5), U4.16 (EN_GATE)
/MCU/FAULT: R32.2, U2.59 (PB7), U4.6 (FAULT)
/MCU/H1: U2.41 (PA8), U4.17 (INH_A)
/MCU/H2: U2.42 (PA9(OTG_FS_VBUS)), U4.19 (INH_B)
/MCU/H3: U2.43 (PA10), U4.21 (INH_C)
/MCU/L1: U2.34 (PB13(OTG_HS_VBUS)), U4.18 (INL_A)
/MCU/L2: U2.35 (PB14), U4.20 (INL_B)
/MCU/L3: U2.36 (PB15), U4.22 (INL_C)
/MCU/LED_GREEN: R9.2, U2.26 (PB0(ADC12_IN8))
/MCU/LED_RED: R8.2, U2.27 (PB1(ADC12_IN9))
/MCU/MISO_ADC_EXT2: R3.1, U2.22 (PA6(ADC12_IN6))
/MCU/SDI: U2.53 (PC12), U4.9 (SDI)
/MCU/SDO: R31.1, U2.52 (PC11), U4.10 (SDO)
/MCU/SENS1: R36.2, R37.2, U2.14 (PA0(ADC123_IN0/WKUP))
/MCU/SENS2: R38.2, R39.2, U2.15 (PA1(ADC123_IN1))
/MCU/SENS3: R40.2, R41.2, U2.16 (PA2(ADC123_IN2))
/MCU/SERVO: C3.2, R11.1, U2.58 (PB6)
/MCU/SLCK: U2.51 (PC10), U4.11 (SCLK)
/MCU/USB_DM: R7.1, U2.44 (PA11)
/MCU/USB_DP: R6.1, U2.45 (PA12)
/MISO_RX_SCL_IN: D1.1 (K), J1.7, R3.2
/Mosfet driver/GH_A: R51.2, R53.2, U4.47 (GH_A)
/Mosfet driver/GH_B: R62.2, R64.2, U4.42 (GH_B)
/Mosfet driver/GH_C: R74.2, R76.2, U4.37 (GH_C)
/Mosfet driver/GL_A: R50.2, R52.2, U4.45 (GL_A)
/Mosfet driver/GL_B: R63.2, R65.2, U4.40 (GL_B)
/Mosfet driver/GL_C: R75.2, R77.2, U4.35 (GL_C)
/Mosfet driver/H1_LOW: C53.2, D10.2 (A), NT1.2, Q2.3 (C), Q5.3 (S), R55.2, R56.2, R57.2, U4.44 (SL_A)
/Mosfet driver/H1_VS: C36.2, C52.2, C55.1, C56.1, D11.2 (A), J8.2 (W), Q3.3 (C), Q4.3 (S), Q5.2 (D), R36.1, R54.2, U4.46 (SH_A)
/Mosfet driver/H2_LOW: C60.2, D13.2 (A), NT3.2, Q7.3 (C), Q9.3 (S), R67.1, R68.2, R69.2, U4.39 (SL_B)
/Mosfet driver/H2_VS: C37.2, C59.2, C63.1, C64.1, D12.2 (A), J8.3 (V), Q6.3 (C), Q8.3 (S), Q9.2 (D), R38.1, R66.1, U4.41 (SH_B)
/Mosfet driver/H3_LOW: C67.2, D15.2 (A), NT5.2, Q11.3 (C), Q13.3 (S), R79.1, R80.2, R81.2, U4.34 (SL_C)
/Mosfet driver/H3_VS: C38.2, C66.2, C68.1, C69.1, D14.2 (A), J8.4 (U), Q10.3 (C), Q12.3 (S), Q13.2 (D), R40.1, R78.1, U4.36 (SH_C)
/OverVoltageProtector/12V: JP1.2 (C), R46.2, U6.8 (VCC)
/OverVoltageProtector/+IN2: R44.1, R45.2, U6.5 (+IN2)
/OverVoltageProtector/-IN2: R42.1, R43.2, U6.6 (-IN2)
/OverVoltageProtector/BRAKE_RTN: D9.A, Q1.2 (C), TP2.1
/OverVoltageProtector/LED+: J7.2 (LED+), R48.1
/OverVoltageProtector/OUT2: Q1.1 (G), R48.2, R49.2, U6.7 (OUT2)
/RX_SDA_IN: D1.4 (K), J1.5, U2.20 (PA4(ADC12_IN4/DAC1_OUT)), U2.30 (PB11)
/SCK_ADC_EXT_IN: D1.5 (K), J1.4, U2.21 (PA5(ADC12_IN5/DAC2_OUT))
/TX_SCL_MOSI_IN: D1.3 (K), J1.6, U2.23 (PA7(ADC12_IN7)), U2.29 (PB10)
GND: C1.2, C2.1, C3.1, C4.2, C5.2, C6.1, C7.2, C8.2, C9.2, C10.2, C11.1, C12.1, C13.1, C14.2, C15.1, C16.1, C17.1, C18.1, C19.1, C20.2, C21.1, C22.2, C24.1, C25.2, C26.1, C27.1, C28.1, C29.1, C30.2, C32.1, C33.1, C34.2, C41.1, C42.1, C43.1, C44.1, C45.1, C46.1, C47.2, C48.1, C49.1, C50.1, C51.1, C54.2, C57.2, C58.1, C61.1, C62.1, C65.2, C70.2, C71.2, D1.2 (A), D2.2 (A), D3.1 (K), D4.1 (K), D5.1 (K), D6.2 (A), D7.2 (A2), J1.3, J2.A1_B12 (GND), J2.B1_A12 (GND), J4.1 (GND), J5.1, J6.1, J7.1 (LED-), J8.1 (GND), J10.2 (B), J11.1 (GND), J12.1 (LED-), J13.1 (GND), NT2.2, NT4.2, NT6.2, P1.1, P2.3 (GND), Q1.3 (E), R1.1, R2.2, R5.1, R18.2, R20.2, R26.2, R30.1, R35.2, R37.1, R39.1, R41.1, R43.1, R45.1, R47.1, R49.1, R56.1, R57.1, R59.1, R61.1, R68.1, R69.1, R71.1, R73.1, R80.1, R81.1, R83.1, R85.1, R88.1, U1.2 (VSS), U1.8 (Rs), U2.12 (VSSA), U2.18 (VSS), U2.60 (BOOT0(VPP)), U2.63 (VSS), U3.4 (V-), U4.28 (AVGND), U4.57 (GND), U5.1 (GND), U6.4 (GND), U7.2 (GND), U8.4 (Vout-), USB1.1 (GND)
NRST: C12.2, P2.5 (NRST), U2.7 (NRST)
unnamed: C1.1, J2.S1 (SHELL_GND), J2.S2 (SHELL_GND), J2.S3 (SHELL_GND), J2.S4 (SHELL_GND)
unnamed: C4.1, R12.2, R13.1
unnamed: C27.2, R28.2
unnamed: C55.2, R58.2, R60.2
unnamed: C56.2, R59.2, R61.2
unnamed: C63.2, R70.2, R72.2
unnamed: C64.2, R71.2, R73.2
unnamed: C68.2, R82.2, R84.2
unnamed: C69.2, R83.2, R85.2
unnamed: D3.2 (A), R8.1
unnamed: D4.2 (A), R9.1
unnamed: D5.2 (A), R10.1
unnamed: C35.2, D6.1 (K), L1.1, U4.50 (PH), U4.51 (PH)
unnamed: C53.1, D10.1 (K), Q2.2 (E), Q5.1 (G), R52.1, R55.1
unnamed: C52.1, D11.1 (K), Q3.2 (E), Q4.1 (G), R53.1, R54.1
unnamed: C59.1, D12.1 (K), Q6.2 (E), Q8.1 (G), R64.1, R66.2
unnamed: C60.1, D13.1 (K), Q7.2 (E), Q9.1 (G), R65.1, R67.2
unnamed: C66.1, D14.1 (K), Q10.2 (E), Q12.1 (G), R76.1, R78.2
unnamed: C67.1, D15.1 (K), Q11.2 (E), Q13.1 (G), R77.1, R79.2
unnamed: D16.2 (A), L2.2, U7.1 (SW)
unnamed: J2.A5 (CC1), R1.2
unnamed: J2.B5 (CC2), R2.1
unnamed: J2.A7 (DN1), J2.B7 (DN2), R7.2, USB1.3 (D-)
unnamed: J2.A6 (DP1), J2.B6 (DP2), R6.2, USB1.2 (D+)
unnamed: J5.3, R11.2
unnamed: C41.2, J10.1 (A), J13.2 (E-STOP), U4.55 (EN_BUCK)
unnamed: J12.2 (LED+), R89.1
unnamed: Q2.1 (B), R50.1
unnamed: Q3.1 (B), R51.1
unnamed: Q6.1 (B), R62.1
unnamed: Q7.1 (B), R63.1
unnamed: Q10.1 (B), R74.1
unnamed: Q11.1 (B), R75.1
unnamed: R21.2, R22.1, U3.1
unnamed: C10.1, U2.5 (PH0-OSC_IN), X1.1
unnamed: C14.1, U2.6 (PH1-OSC_OUT), X1.2
unnamed: C8.1, U2.31 (VCAP1)
unnamed: C9.1, U2.47 (VCAP2)
unnamed: R23.2, R25.1, U3.3 (+)
unnamed: R22.2, R24.1, U3.2 (-)
unnamed: C20.1, R19.2, R20.1, U3.5 (+)
unnamed: R23.1, U3.6 (-), U3.7
unnamed: C32.2, U4.27 (AVDD)
unnamed: C36.1, U4.48 (BST_A)
unnamed: C37.1, U4.43 (BST_B)
unnamed: C35.1, U4.52 (BST_BK)
unnamed: C38.1, U4.38 (BST_C)
unnamed: C29.2, R28.1, U4.2 (COMP)
unnamed: C31.2, U4.14 (CP1)
unnamed: C31.1, U4.15 (CP2)
unnamed: R30.2, U4.7 (DTC)
unnamed: C30.1, U4.23 (DVDD)
unnamed: C22.1, C25.1, U4.13 (GVDD)
unnamed: R35.1, U4.1 (RT_CLK)
unnamed: R33.2, U4.25 (S01)
unnamed: R34.2, U4.26 (S02)
unnamed: C34.1, U4.56 (SS_TR)
unnamed: R26.1, R27.2, U4.3 (VSENSE)
unnamed: R46.1, R47.2, U6.3 (+IN1)
unnamed: U6.1 (OUT1), U6.2 (-IN1)
unnamed: R86.1, U7.4 (EN)
unnamed: R87.1, R88.2, U7.3 (FB)
PA15: J9.8, U2.50 (PA15(JTDI))
PB2: J9.1, U2.28 (PB2-BOOT1)
PB3: J9.9, U2.55 (PB3(JTDO/TRACESWO))
PB4: J9.10, U2.56 (PB4(NJTRST))
PB12: J9.2, U2.33 (PB12)
PC5: J9.3, U2.25 (PC5(ADC12_IN15))
PC13: J9.4, U2.2 (PC13_(RTC_AF1))
PC14: J9.6, U2.3 (PC14-OSC32_IN)
PC15: J9.7, U2.4 (PC15-OSC32_OUT)
PD2: J9.5, U2.54 (PD2)
SNA: C39.2, NT1.1, U4.33 (SN2)
SNB: C40.1, NT3.1, U4.31 (SN2)
SNC: C23.1, NT5.1, R24.2
SPA: C39.1, NT2.1, U4.32 (SP1)
SPB: C40.2, NT4.1, U4.30 (SP2)
SPC: C23.2, NT6.1, R25.2
SWCLK: P2.2 (SWCLK), U2.49 (PA14(JTCK-SWCLK))
SWDIO: P2.4 (SWDIO), U2.46 (PA13(JTMS-SWDIO))
VCC: C11.2, C13.2, C15.2, C16.2, C17.2, C18.2, C19.2, C24.2, C47.1, C49.2, C50.2, C51.2, D1.6 (K), J1.2, NTC1.1, P2.1 (Vcc), R10.2, R14.2, R15.2, R16.2, R17.2, R19.1, R29.2, R31.2, R32.1, U1.5 (Vref), U2.1 (VBAT), U2.13 (VDDA), U2.19 (VDD), U2.32 (VDD), U2.48 (VDD), U2.64 (VDD), U3.8 (V+), U4.24 (REF), U4.49 (VDD_SPI), U5.2 (VO)
V_SUPPLY: C33.2, C42.2, C54.1, C57.1, C58.2, C61.2, C62.2, C65.1, D8.1 (K), D9.C (K), J11.2 (48V), Q4.2 (D), Q8.2 (D), Q12.2 (D), R4.1, R44.2, R58.1, R60.1, R70.1, R72.1, R82.1, R84.1, TP3.1, U4.29 (PVDD1), U4.53 (PVDD2), U4.54 (PVDD2)

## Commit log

2024-05-02 Modified for OpenFFBoard.
    [12VBoost.kicad_sch, 12VBoostModule.kicad_sch, CAN.kicad_sch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]
2024-05-02 Removed Firmware Folder.
    [pi_stm32.cfg, stm32-bv_openocd.cfg]
2024-05-17 Error fix.
    [5XBomLcsc.csv, bom.csv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]
